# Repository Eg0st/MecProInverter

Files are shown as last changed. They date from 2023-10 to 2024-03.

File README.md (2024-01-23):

# Goal
This project is a student project at the Munich University of Applied Sciences.
The aim is to build and operate an inverter with an output of 3.6 kW,
which is supplied with 230 volts and can operate a motor in the frequency range of 10 to 500 Hz.
The ESP32-S3 and the SimpleFoc Bilbiotek were used for this.

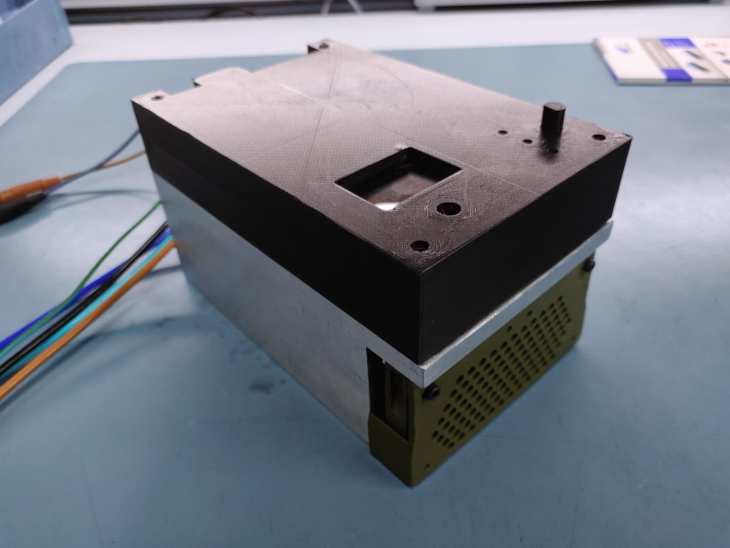
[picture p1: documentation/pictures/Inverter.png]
Inverter


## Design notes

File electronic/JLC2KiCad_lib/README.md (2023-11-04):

# MecProInverter

## ECAD Library
The Library is generatet via JLC2KiCad python skript from the JLCPCB assembly library. 
https://github.com/TousstNicolas/JLC2KiCad_lib

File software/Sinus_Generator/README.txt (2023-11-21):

Kleine Sinus Generator Klasse

erstellt einen Sinus, von -+256, es werden Werte von 0 bis PI/2 erstellt
die restliche Berechnung erfolgt unter Ausnutzung des Zweierkomplements,
da es ein periodisches Signal ist

Zweck: Vergleich für einen PWM Timer, um die Drehzahl abzulaufen

PS: wenn einer einen Plan hat wie man einen Konstruktor constexpr anlegt,
mir gerne Bescheid sagen ;D

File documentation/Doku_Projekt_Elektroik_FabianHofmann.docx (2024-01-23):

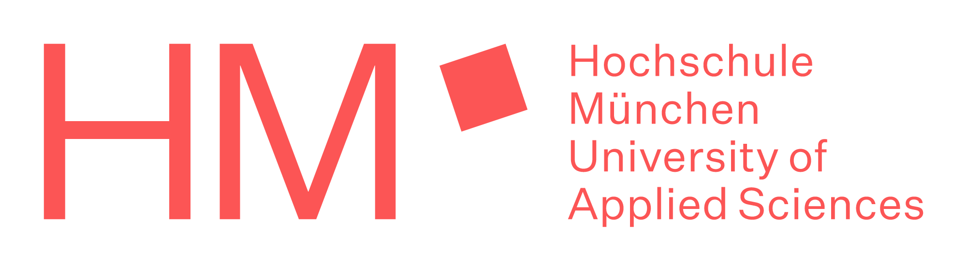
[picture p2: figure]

# Mechatronik Projekt- Entwicklung und Herstellung eines Umrichters für Drehstrommaschinen

Fabian Hofmann: Mechanik – Thermische Belastung und Gehäuse

# Elektronik

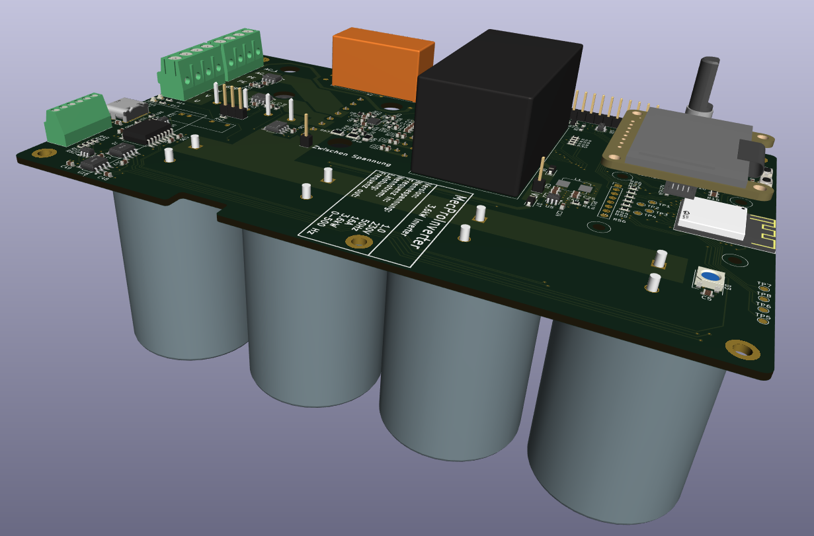
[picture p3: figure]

# 1. Abbildungsverzeichnis

# 2. Einführung

## Ziele

Ziel dieses Projektes war die Entwicklung und der Bau eines 3,6 kW Wechselrichters. Dieser sollte folgende Anforderungen erfüllen.

- Eingangsleistung von 3,6 kW (einphasig)
- Ausgang drei Phasen
- Ausgangs Frequenz variable von 10 bis 500 Hz
- Professionale Verarbeitung

Das gesamte Projekt wird Open Source sein, so dass Interessierte das Projekt replizieren können. Das Projekt ist in folgenden GitHub Repository vollständig einsehbar: https://github.com/Eg0st/MecProInverter

Da das Konzept einige Besonderheiten aufweist, sollte vor der Inbetriebnahme das Kapitel „Inbetriebnahme“ gelesen werden.

## Lösungsansatz

Der Inverter basiert auf einer 3-Fach-Halbbrücke. Dabei wird die Wechselspannung zunächst über einen Brückengleichrichter gleichgerichtet und in den Zwischenkreiskondensatoren, hier mit C1 bezeichnet, geglättet. Anschließend wird aus der Gleisspannung mit der 3-Fach-Halbbrücke ein sinuskommutiertes PWM-Signal erzeugt. Wird dieses Signal auf einen Drehstrommotor gegeben, so erzeugt die große Induktivität in dem Motor einen Sinus aus der PWM.

Abbildung 1 Konzept Plan

Für die Steuerung sind weitere Komponenten wie z.B. ein Mikrocontroller erforderlich.

# 3. Konzepte

## GitHub Repository

Die kompletten Daten sind im GitHub Repository verfügbar. Hier befindet sich die komplette Elektronik in den Ordnern „MecProInverter\electronic“. Das KiCad Projekt befindet sich im Ordner „MecProInverter\electronic\MecProInverter“. Die verwendeten Bibliotheken befinden sich in den Ordnern own_library und JLC2KiCad_lib. Own_library enthält alle selbst erstellten Bibliotheken und JLC2KiCad enthält alle Bibliotheken, die über das Phython Skript JLC2KiCad erstellt wurden. Dieses Skript ermöglicht es von Komponenten von JLCPCB eine Bibliothek für KiCad herunterzuladen.

## Isolationskonzept

Um die Kosten niedrig zu halten, wurde beschlossen, die gesamte Elektronik bis auf wenige Ausnahmen nicht gegeneinander zu isolieren. Lediglich der USB-Anschluss und vier GPIO-Pins sind isoliert. Dies spart Kosten und Aufwand, ermöglicht aber trotzdem die Nutzung aller Funktionen. Daher muss das komplette Human-Interface gegen Berührung isoliert werden, um eine sichere Bedienung sicherzustellen. Das wird durch Plastik Verlängerungen der Taster etc. erreicht.

## Stromversorgung

Während des normalen Betriebes wird das ganze System über die Netzspannung versorgt. Jedoch werden für die Steuerung zwei Hilfsspannungen benötigt.

- 15 Volt
- 3,3 Volt

Aus der Netzspannung von 230 Volt werden mit Hilfe eines Fertigmoduls 15 Volt mit bis zu 1,2 Ampere erzeugt. Aus den 15 Volt werden mit einem DC/DC-Wandler 3,3 Volt erzeugt. Zusätzlich kann der 3,3 Volt Regler über den VBus des USB-Anschlusses versorgt werden.

## Auslegung Zwischen Kreis

Der Zwischenkreis wurde nachfolgender Formel ausgelegt. Es wurde mit einer Schaltfrequenz des IGBT von 10 kHz gerechnet.

C=1/(∆U)*I*t

Daraus ergibt sich eine erforderliche Gesamtkapazität von 3 mF. Um Kosten zu sparen und den Platz besser zu nutzen, wurden drei 1 mF 325 Volt Kondensatoren parallelgeschaltet. Zur Sicherheit wurde der Einbauplatz für einen vierten vorbereitet.

# 4. Schaltplan

Der Schaltplan ist in zwei Teile gegliedert. Ein Teil enthält die gesamte Leistungselektronik und der zweite Teil enthält die Steuerung und Kommunikation. Dazu wurden in KiCad 7.0 zwei Pages erstellt. Die Power Page enthält die Leistungselektronik und die Controller Page den Rest. Im folgenden Kapitel wird auf alle Schaltungskomponenten eingegangen wobei der Schalplan im GitHub Repository zu finden ist. Die Datenblätter zu allen verwendeten Komponenten befinden sich im GitHub Ordner „GitHub\MecProInverter\electronic\datasheet“.

## Controller

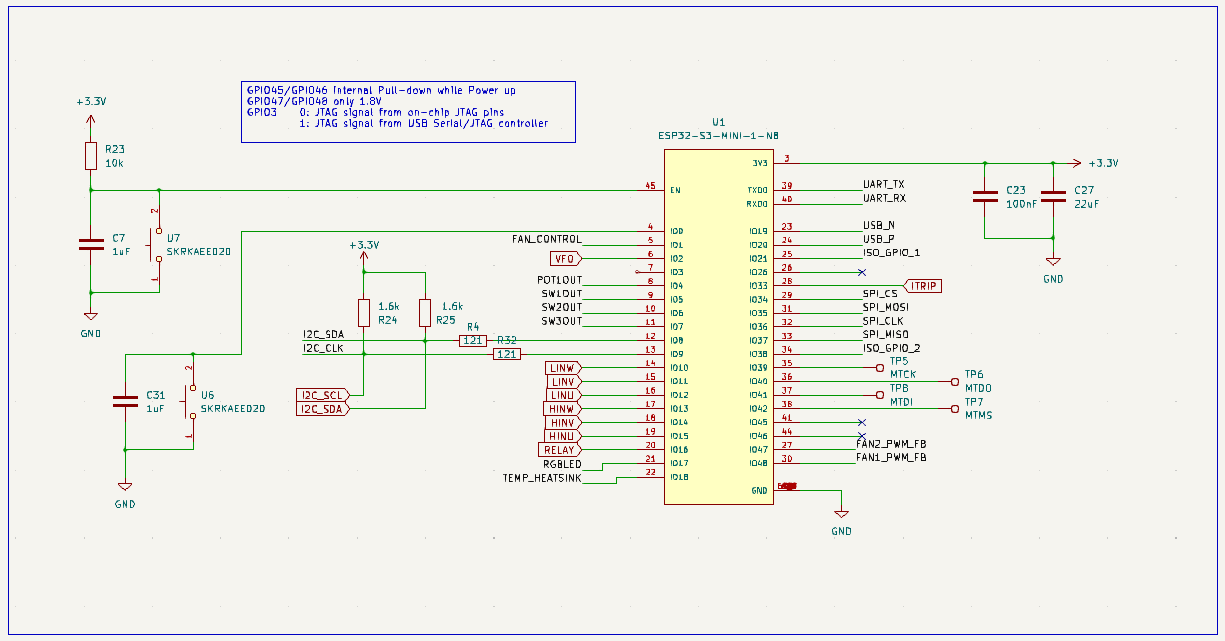
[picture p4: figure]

Abbildung 2 Mikrocontroller-Schaltung

Als Controller kommt der ESP-S3 Mini zum Einsatz. Dieser bietet neben dem notwendigen MPWM-Modul auch eine direkte USB-Schnittstelle. Dadurch kann auf einen Serial to USB-Konverter verzichtet werden. Am Enabele Pin befindet sich ein Reset Taster, der über einen Pull Up Widerstand auf High gehalten wird. Dadurch kann der Controller bei Bedarf neu gestartet werden. Darunter befindet sich am GPIO-Pin 0 der Mood Taster. Solange dieser beim Start des Controllers gedrückt wird, startet dieser in den Bootmodus und kann programmiert werden.

## Steuerung

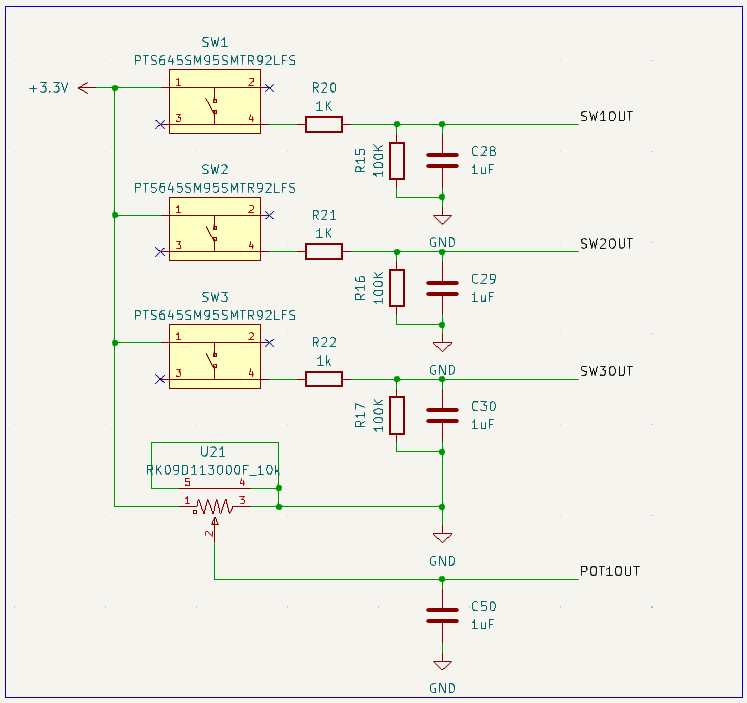
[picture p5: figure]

Abbildung 3 Steuerungs-Schaltung

Der Wechselrichter ist mit drei Tastern und einem Potentiometer zur Bedienung ausgestattet. Mit dem Potentiometer kann die Frequenz eingestellt werden. Die drei Taster sind für die restliche Steuerung und Navigation im internen Menü vorgesehen. Im Zusammenspiel mit dem Display soll es möglich sein, auch detailliertere Einstellungen vorzunehmen. Die Taster sind so beschaltet, dass sie den Pin des Controllers auf 3,3 Volt ziehen. Zusätzlich werden sie über ein RC-Glied entprellt. Dieses RC-Glied hat eine Einschaltverzögerung von 5 ms. Der Kondensator C50 sorgt dafür, dass die Spannung am Potentiometer geglättet wird.

## Anzeige

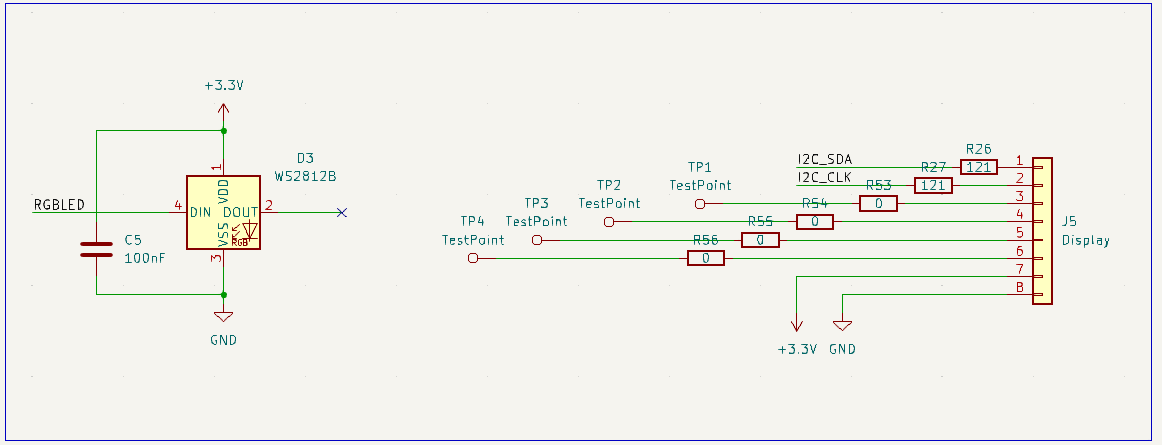
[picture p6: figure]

Abbildung 4 Anzeige-Schaltung

Der Inverter verfügt über ein Display und eine RGB-LED zur Statusanzeige etc. Die RGB-LED ist wie ein Schieberegister programmiert und kann über den DOUT mit weiteren LEDs verbunden werden. Zu beachten ist, dass der Betrieb der LED eine Versorgungsspannung von 3,5 Volt benötigt, es ist aber auch möglich, die LED mit 3,3 Volt zu betreiben. Für das Display wird ein I2C Display mit der Bezeichnung 938 der Firma Adafruit verwendet. Es handelt sich um ein 1“3 Zoll Oled Display.

## Kommunikation

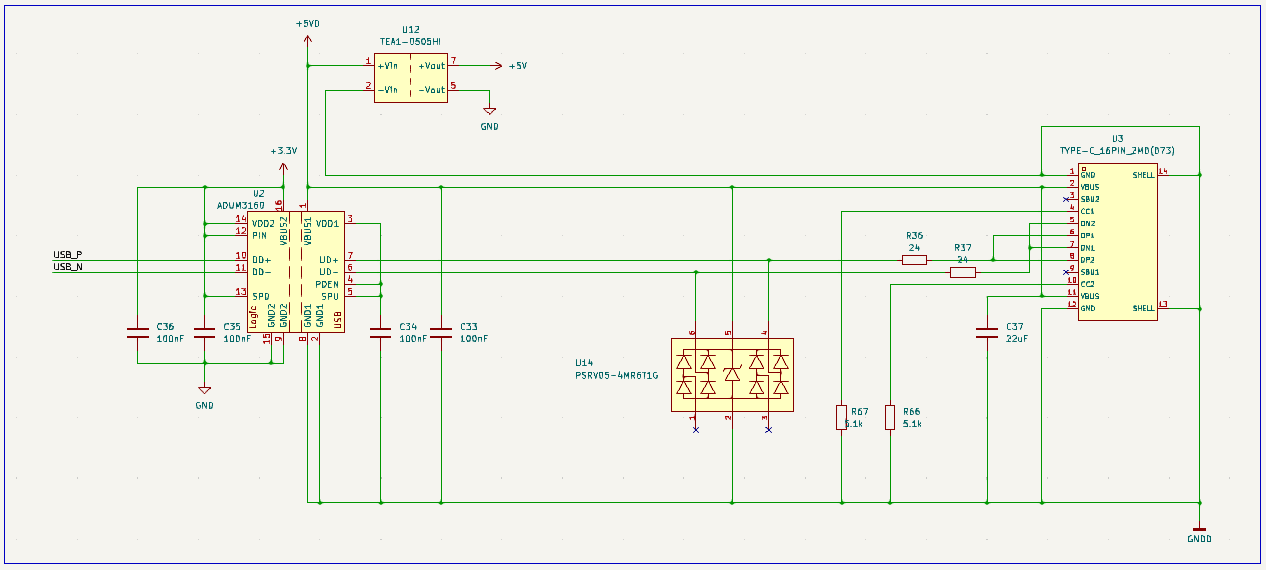
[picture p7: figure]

Abbildung 5 USB-C-Schaltung

Der Controller kann über eine isolierte USB-C-Buchse programmiert werden. Zusätzlich versorgt die USB-Schnittstelle über einen isolierten DC/DC-Wandler den 3,3 Volt Spannungswandler, so dass der Controller auch ohne zusätzliche Spannungsquelle betrieben und programmiert werden kann. Die isolierte USB-Schnittstelle bietet zudem den Vorteil, dass der Controller auch während des normalen Betriebs ausgelesen werden kann. Um einen Mindestschutz gegen ESD-Schäden zu gewährleisten, ist der USB-Eingang mit kurzangeschlossenen ESD-Dioden ausgestattet.

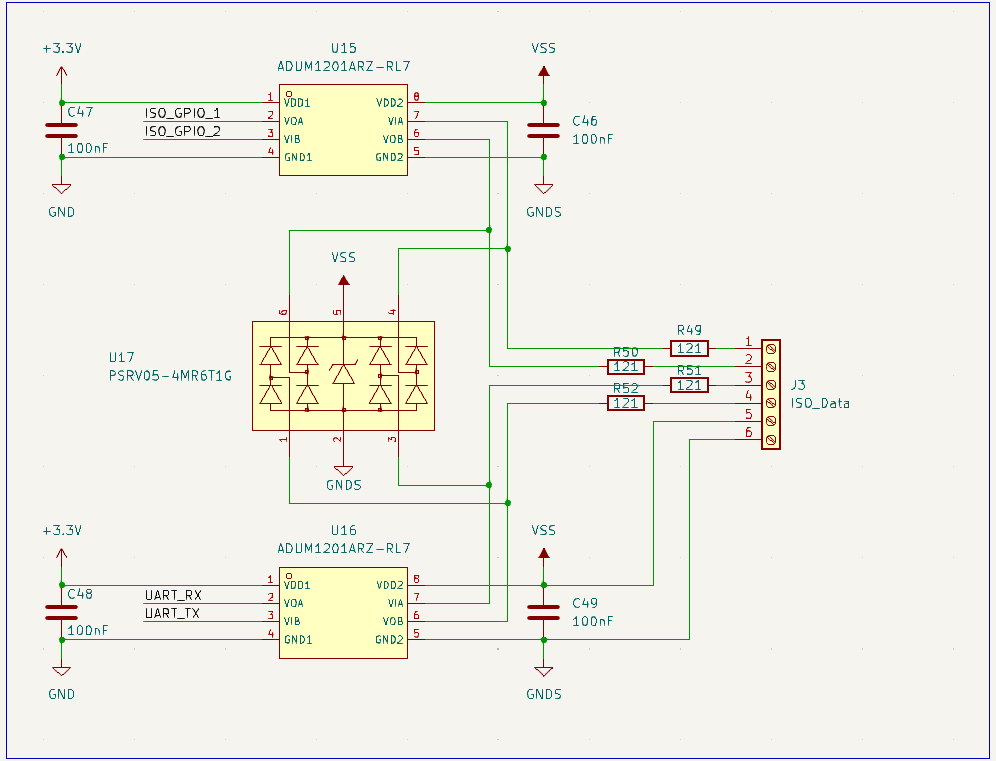
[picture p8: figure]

Abbildung 6 Isolierte GPIO Pin Schaltung

Neben der USB-Schnittstelle verfügt der Inverter über weitere isolierte Datenein- und -ausgänge. Darunter befinden sich eine UART-Schnittstelle sowie zwei freie GPIO-Pins. Da der ESP-32 eine freie Wahl der PINs für die Logikschnittstellen bietet, ist es somit möglich, an diesen beiden Pins eine isolierte I2C-Schnittstelle etc. zu realisieren. Diese Schnittstelle kann für eine externe Steuerung oder für einen externen Sensor verwendet werden. Eine weitere Anwendung wäre ein Not-Aus-Schalter.

## Lüfter Steuerung

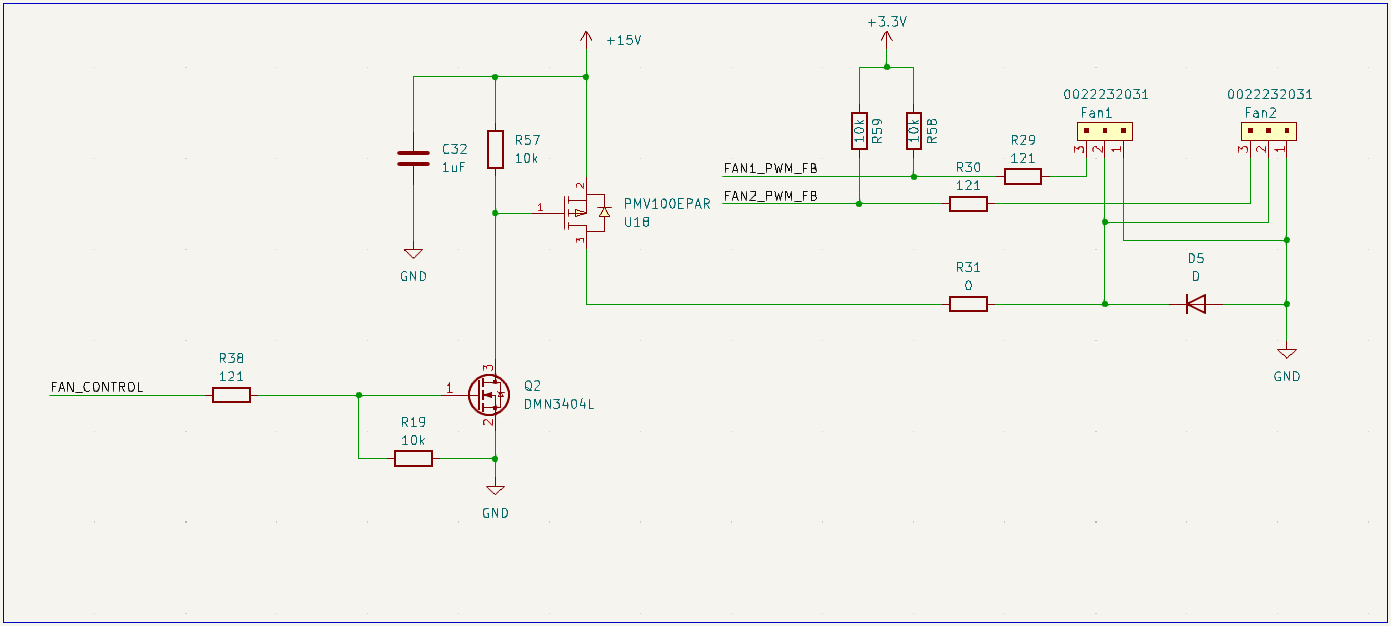
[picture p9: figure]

Abbildung 7 Lüftersteuerung-Schaltung

Die beiden Lüfter zur Kühlung des Kühlkörpers sind parallelgeschaltet und können daher nur synchron geschaltet werden. Jeder hat jedoch einen eigenen PWM-Rückmeldeausgang. Damit kann sichergestellt werden, dass kein Lüfterfehler vorliegt. Die Ansteuerung der Lüfter sollte zunächst über ein PWM-Signal erfolgen, jedoch ist eine normale PWM-Ansteuerung bei den verwendeten Lüftern nicht möglich, da diese eine reine Gleichspannung zum Betrieb benötigen. Zu beachten ist auch, dass die Lüfter Highside geschaltet werden müssen, da sonst der PWM-Regelkreis nicht funktioniert. R31 ist für den Fall vorgesehen, dass die Versorgung der Lüfter mit mehr als 15 Volt zu Störungen führt. Die Spannung kann durch einen Vorwiderstand auf 12 Volt reduziert werden.

## Pree-Charge

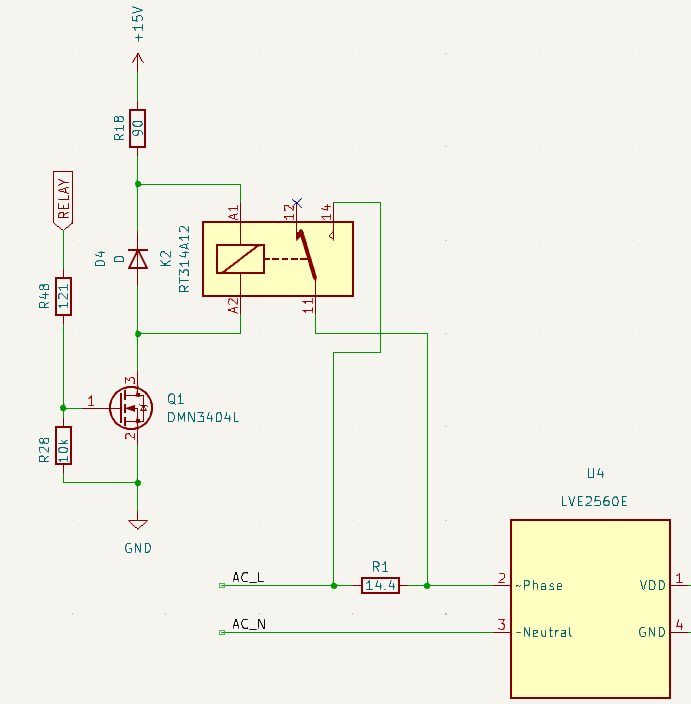
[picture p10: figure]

Abbildung 8 PreeCharge-Schaltung

Die Vorladung dient zur Begrenzung des Einschaltstromes beim Einschalten des Gerätes. Ohne Pre-Charging werden die Zwischenkreiskondensatoren direkt an die Netzspannung angeschlossen, diese stellen im ersten Moment einen Kurzschluss dar, wodurch der maximal mögliche Strom abfällt. Im schlimmsten Fall kann der hohe Strom die interne Schaltung des Zwischenkreises beschädigen. Deshalb werden die Kondensatoren über einen Widerstand geladen. Sobald die Kondensatoren geladen sind, wird der Widerstand durch ein Relais überbrückt. Andernfalls würde unnötig Energie verschwendet. Das Relais ist normal offen und wird vom Mikrocontroller über einen Mosfet auf der Lowside geschaltet. Die Diode D4 wird benötigt, um mögliche Rückinduktionsströme, die beim Abschalten des Relais entstehen, kurzzuschließen. R18 wird als Vorwiderstand benötigt, da es sich bei dem Relais um ein handelsübliches und somit kostengünstiges 12-Volt-Relais handelt.

## Messungen

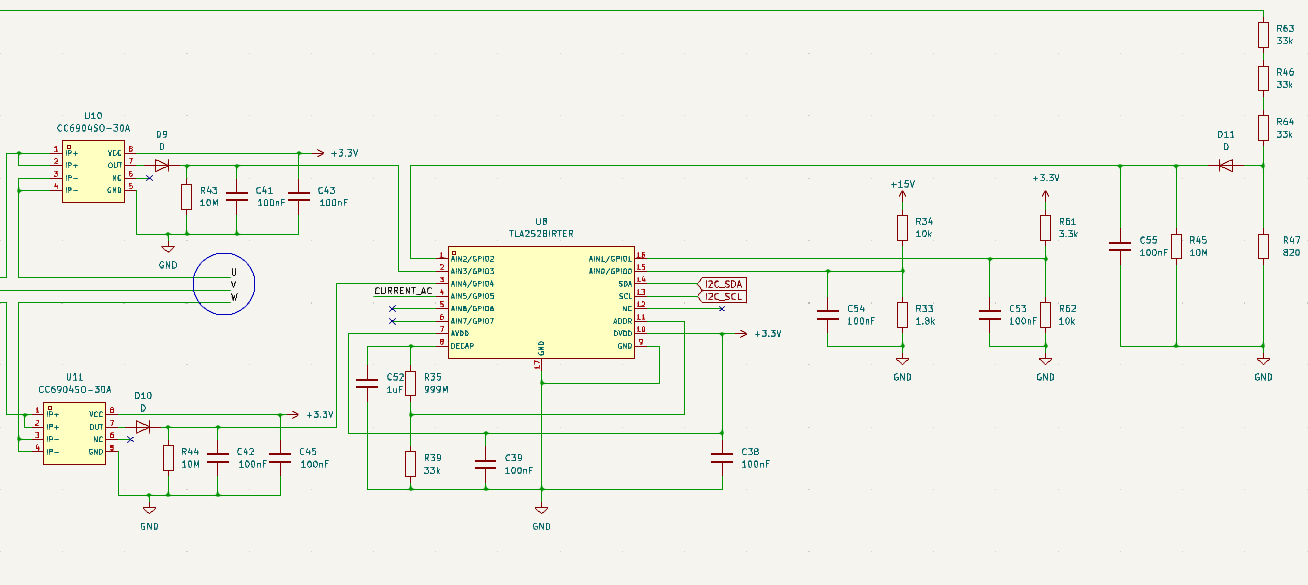
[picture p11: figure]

Abbildung 9 ADC und Hallsensor-Schaltung

Da der ESP32-S3 nur einen 12 Bit ADC mit großem Offset besitzt, wurde beschlossen, einen externen 8 Kanal ADC zu installieren. Dieser misst folgende Werte:

- Zwischenkreisspannung
- 3,3 Volt
- 15 Volt
- Eingangsstrom
- Ausgangstrom an der Phase U und W

Der ADC ist über I2C mit dem Mikrocontroller verbunden. Die Spannungsteiler für die Spannungsmessung sind so ausgelegt, dass sie bei Nennspannung eine Spannung von 2,5 Volt erzeugen. Außerdem besitzen sie alle einen Kondensator zur Spannungsglättung. Die Zwischenkreisspannung wird durch eine Diode und einen Kondensator gemessen. Der Widerstand R45 dient zur Entladung des Kondensators, um auch einen länger andauernden Spannungsabfall an der Zwischenkreisspannung messen zu können. Bei der Zwischenkreismessung wurden mehrere Widerstände in Reihe geschaltet, um die maximale Spannung der Widerstände nicht zu überschreiten.

Um den Strom auch auf der High Side messen zu können, werden Hallsensoren verwendet, die in Abhängigkeit vom Strom eine Spannung ausgeben. Da die verwendeten Sensoren einen Offset besitzen, kann mit ihnen auch ein negativer Strom gemessen werden. Diese Sensoren werden ebenfalls an den externen ADC angeschlossen. Mit dem Maschensatz kann der Strom der letzten Phase W genau berechnet werden.

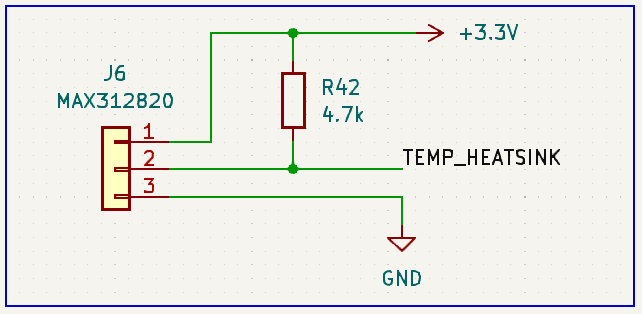
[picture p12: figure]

Zur Messung der Kühlkörpertemperatur ist zusätzlich ein Steckplatz für einen One-Wire Temperatursensor vorbereitet. Dieser wird jedoch nicht benötigt, da das verwendete Powermodul über einen internen Temperatursensor verfügt.

## Stromversorgung

Für den Betrieb der Schaltung sind zwei Hilfsspannungen erforderlich. Zum einen 15 Volt für den Betrieb des IGBT, des Lüfters und des Relais. Zusätzlich werden 3,3 Volt für den Betrieb des Mikrocontrollers und der Peripherie benötigt. Aus den 230 Volt Wechselspannung werden also mit einem fertigen Modul 15 Volt erzeugt. Aus diesen werden dann über einen DC/DC-Wandler 3,3 Volt erzeugt. Zusätzlich ist es möglich, den 3,3 Volt DC/DC Wandler über die 5 Volt des USB-Anschlusses zu versorgen. Dazu wurden Dioden so eingebaut, dass sich die beiden Spannungsquellen nicht gegenseitig beeinflussen. J9 ist ein Messpunkt für.

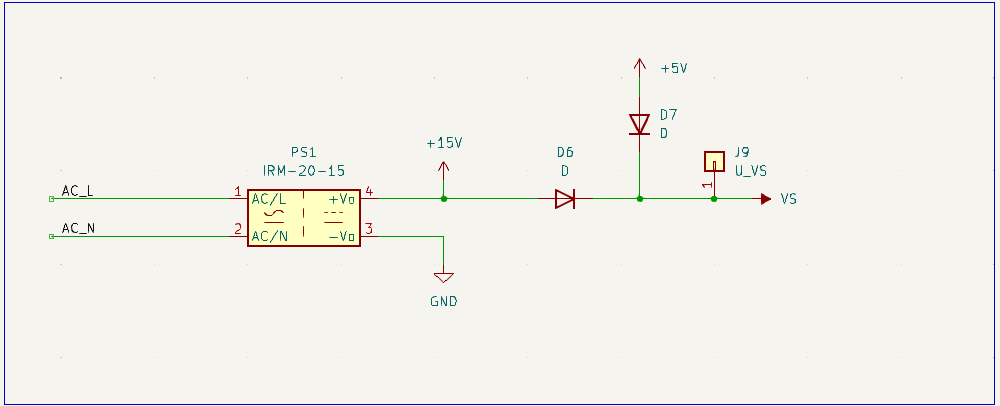
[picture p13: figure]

Abbildung 10 Parallelschaltung Stromquellen-Schaltung

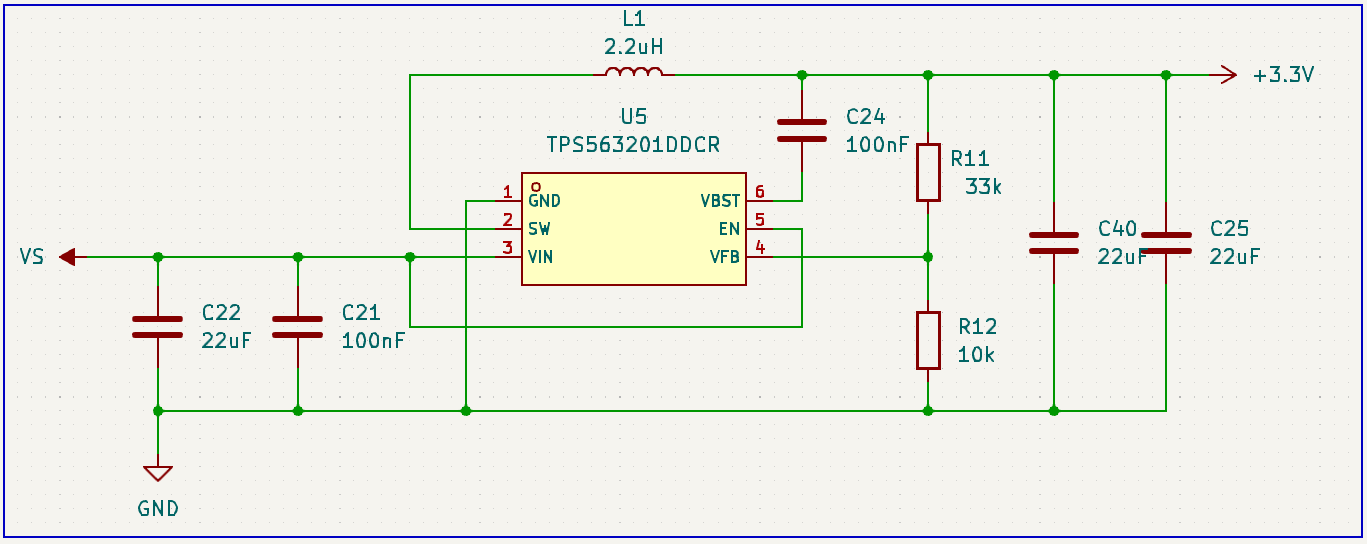
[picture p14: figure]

Abbildung 11 3,3 Volt Regler-Schaltung

Der Aufbau der 3,3 Volt DC/DC Wandler (TPS563201DDCR) ist dem Datenblatt entkommen. Die Spannung kann mithilfe der Widerstände R11 und R12 eingestellt werden.

## IGBT

Als Leistungsmodul kommt der IKCM20L60GA der Firma Infineon zum Einsatz. Dabei handelt es sich um eine Triple-H-Brücke mit integriertem Treiber. Dies hat den Vorteil, dass für den Betrieb nur eine minimale Anzahl von Bauteilen benötigt wird. Zusätzlich bietet das Modul die Möglichkeit, den aktuellen Betriebszustand bzw. die Temperatur über einen analogen Pin auszulesen. Zusätzlich kann über den ITRIP-Pin eine Strombegrenzung realisiert werden. Im Projekt wird der Pin direkt vom Mikrocontroller angesteuert, um das Modul im Fehlerfall abzuschalten.

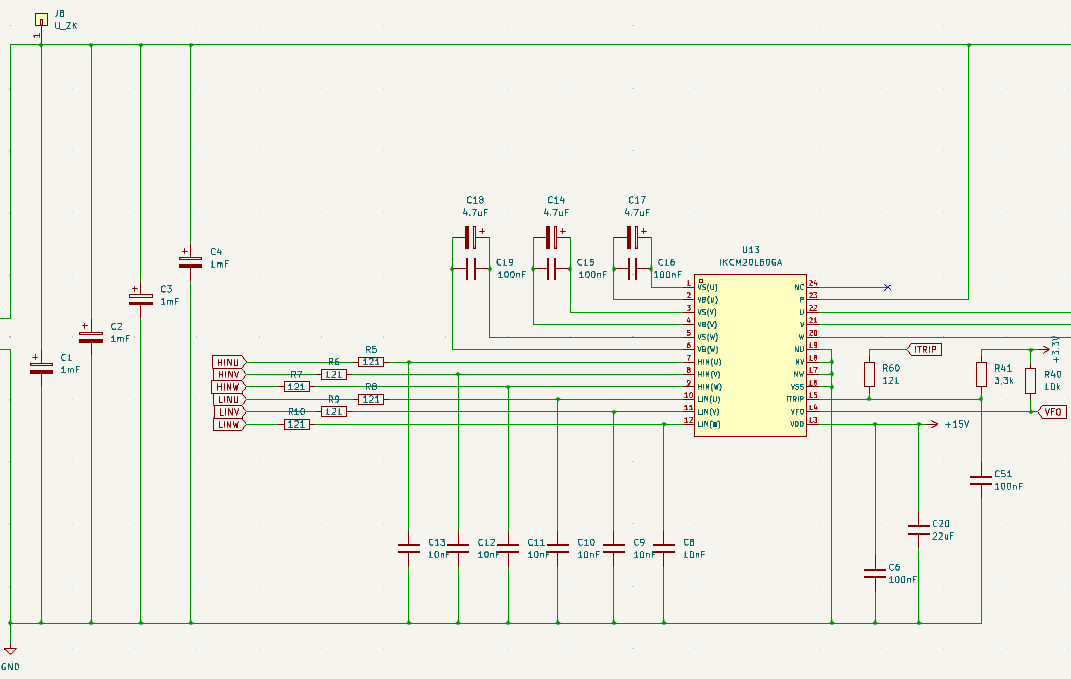
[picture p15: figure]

Abbildung 12 IGBT-Schaltung

C1 bis C4 sind die Zwischenkreiskondensatoren und werden über das Netz auf ca. 325 Volt geladen. Die einzelnen MosFests werden über HINU, HINV, ... angesteuert. Diese haben eine Strombegrenzung, die mit Widerständen realisiert ist, um den Mikrocontroller zu schonen. C14 bis C19 dienen als Kondensator zur Erzeugung der Spannung zum Schalten der Highside Kondensatoren. Diese werden aufgeladen, wenn die Low Side Gates durchgeschaltet werden. Daher ist es nicht möglich, die High Side Gates von Anfang an durchzuschalten. Die weitere Schaltung ist dem Datenblatt bzw. der Application Note zu entnehmen.

# 5. Layout

Das Layout wurde in KiCad erstellt. Das Layout besteht aus 4 Ebenen. In der Darstellung ist die Oberseite rot und die Unterseite blau dargestellt. Die Zwischenlängen wurden hauptsächlich als Grundriss und für die Spannungsversorgung verwendet. Die Spannungsversorgung ist hier jedoch je nach Bedarf in mehrere Bereiche unterteilt. Zusätzlich befindet sich in der rechten oberen Ecke ein Isolierbereich für isolierte Anschlüsse. Der Isolationsabstand zwischen den einzelnen Spannungsebenen beträgt 0,8 mm. Zu den isolierten Bereichen sind Abstände von 4 mm vorgesehen.

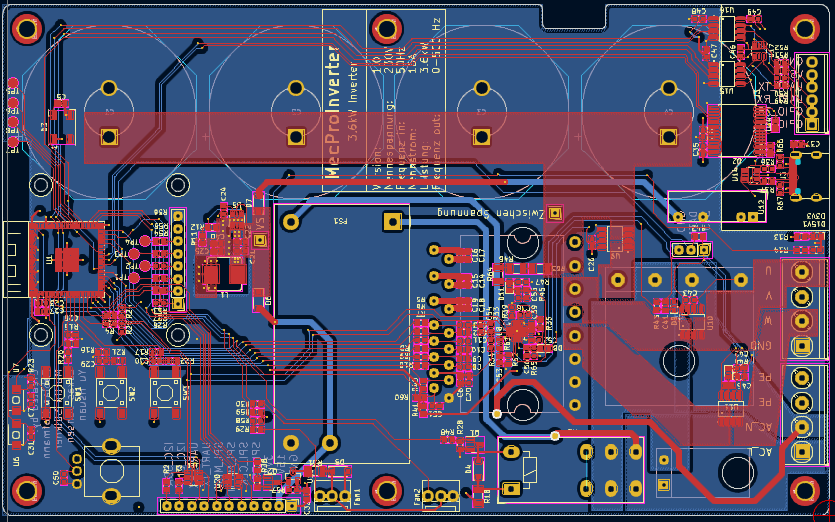
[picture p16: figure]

Abbildung 13 Layout (Ohne Zwischen Lagen)

Die Platine ist so aufgebaut, dass die einzelnen Komponenten wie Leistungselektronik, DC/DC-Wandler, Logikschaltungen möglichst getrennt sind.

Zu beachten ist auch, dass sich unterhalb der Antenne des ESP32-S3 keine Platine befinden darf, da dies die Performance des WLAN-Moduls beeinträchtigt. Für die mechanische Befestigung der Leistungsbauteile auf dem Kühlkörper sind zusätzliche Bohrungen vorgesehen. Die Aussparung auf der Oberseite dient als Kabeldurchführung für die Lüfter.

Es ist jedoch zu beachten, dass der Footprint des Brückengleichrichters nicht korrekt ist. Dieser ist seitenverkehrt und muss für eine V2 überarbeitet werden.

# 6. Inbetriebnahme

Die erste Inbetriebnahme ist durch Einstecken des USB-Steckers möglich. Dabei sollte bereits die 3,3 Volt LED aufleuchten. Außerdem sollte es möglich sein, den Micocontroller zu programmieren und die IOs anzusteuern.

Im nächsten Schritt kann über den 15 Volt Pin eine externe 15 Volt Spannungsquelle angeschlossen werden. Nun können die Lüfter, das Relais und der IGBT angesteuert werden und die 15 Volt LED sollte leuchten. Wird nun eine Spannung über den Zwischenkreis-Pin eingespeist, kann der IGBT am Ausgang getestet werden. Dabei ist zu beachten, dass zum Ansteuern der High-Treiber des IGBTs zunächst der Versorgungskondensator für die Treiber aufgeladen werden muss. Dies geschieht, sobald die Low-Treiber der einzelnen Phasen durchgeschaltet sind. Um den IGBT zu testen, ist es daher sinnvoll, ein PWM-Signal anzulegen. Um die Ausgänge des IGBT zu aktivieren, muss der ITRIP-Pin auf Low gesetzt werden.

Im letzten Schritt können 230 Volt angelegt werden. Dabei muss jedoch die 15 Volt Hilfsspannung abgeschaltet werden. Dabei ist zu beachten, dass der Vorladewiderstand ggf. über den Kühlkörper gekühlt oder anderweitig überbrückt werden muss. Alternativ kann die Spannung durch einen regelbaren Trenntransformator etc. langsam erhöht werden.

Da der USB-Anschluss isoliert ist kann bei jedem Schritt der Status des Inverters über den Micocontroller überwacht werden.

# 7. Tests

Alle Komponenten mit einer Versorgungsspannung von bis zu 15 Volt wurden auf Funktion getestet. Alles funktionierte wie erwartet und sind deshalb nicht interessant. Daher wird in diesem Kapitel nur Versuche dokumentiert, die bei höheren Spannungen durchgeführt wurden. Es wurden folgende zwei Versuche durchgeführt.

## Versorgung über 230 Volt an einem Trenntransformator

Der Wechselrichter wurde an den Trenntransformator angeschlossen und die Spannung langsam erhöht. Damit sollte sichergestellt werden, dass die Spannungsversorgung funktioniert und kein Kurzschluss vorliegt. Dazu wurde die Zwischenkreisspannung extern mit einem Multimeter gemessen.

Es ist zu beobachten, dass die Spannung am Zwischenkreis mit steigender Eingangsspannung zunimmt. Wobei diese um einen Faktor von ca. 1,4 höher ist. Dies ist auf die Gleichrichtung der Wechselspannung zurückzuführen. Ab einer Spannung von ca. 100 Volt schaltet der 15 Volt und 3,3 Volt Spannungskreis. Eine weitere Erhöhung der Spannung führt nur zu einer Änderung der Zwischenkreisspannung.

## Ansteuerung des IGBT bei 100 V mit PWM-Sinuskommutierung

In diesem Versuch soll die PWM-Sinuskommutierung am Ausgang des IGBT überprüft werden. Dazu wird der Wechselrichter über einen Trenntrafo mit Spannung versorgt. Die Spannung wird so gewählt, dass alle Komponenten funktionieren (15 Volt Regler). Nun wird mit Hilfe eines Oszilloskops der unbelastete Ausgang des Wechselrichters betrachtet. Dabei wurden die einzelnen Phasen es Ausgangs gegen Masse dargestellt.

Die folgenden Spannungsverläufe wurden zu verschiedenen Zeitpunkten aufgezeichnet. Am Zwischenkeil wurde eine Spannung von 100 Volt gemessen.

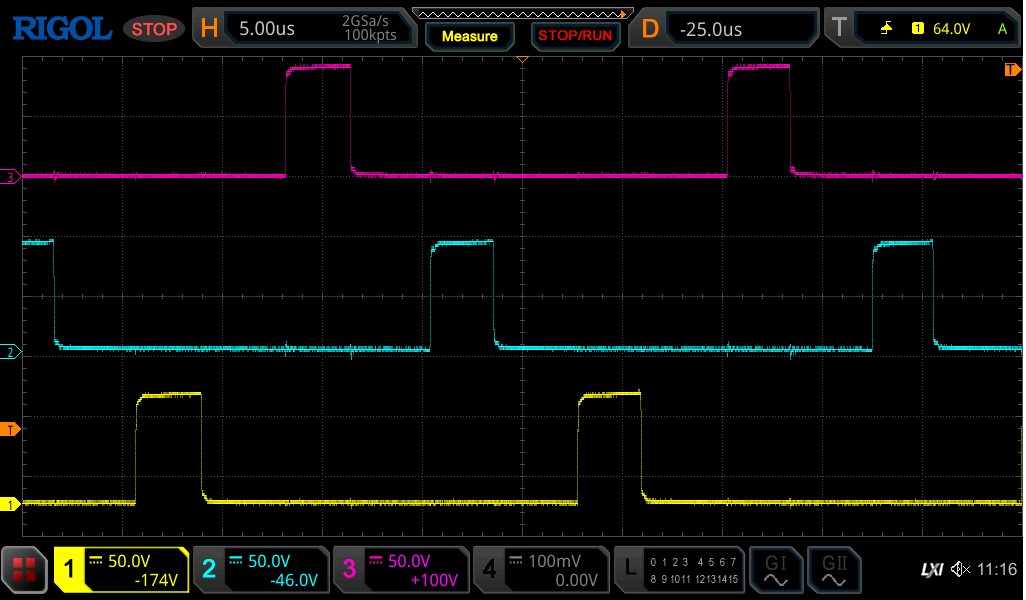
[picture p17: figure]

Abbildung 14 Testergebnis Einschaltdauer ca. 20

Es ist gut zu erkennen, dass der IGBT bis zu den 100 Volt des Zwischenkreises voll durchschaltet und auch gegen Masse schaltet.

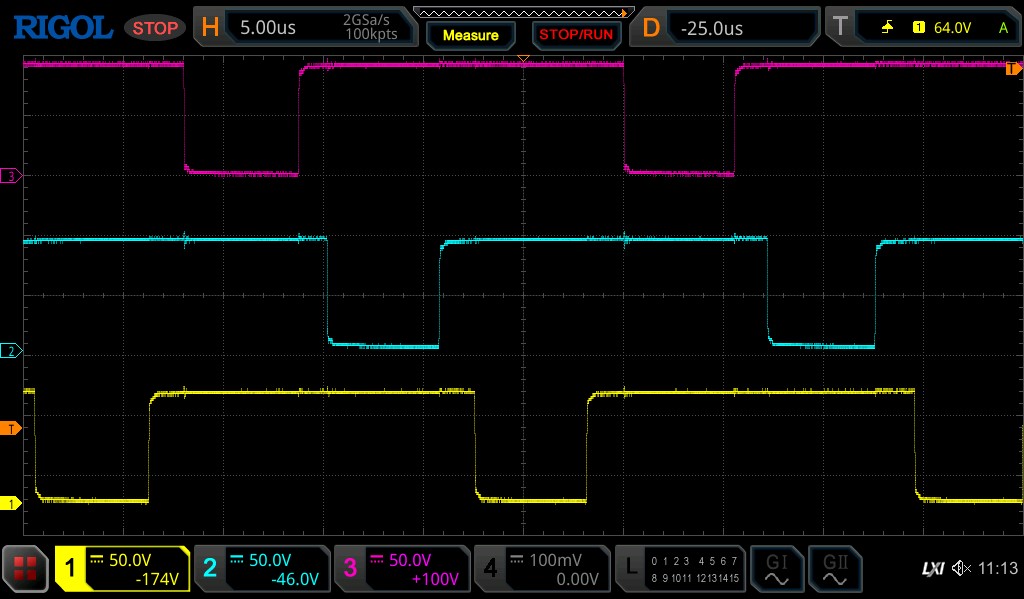
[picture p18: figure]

Abbildung 15 Testergebnis Einschaltdauer ca. 80

Dieser Abschnitt wurde zu einem späteren Zeitpunkt hinzugefügt. Durch die Änderung der Steuerzeiten ist anzunehmen, dass die PWM-Sinuskommutierung funktioniert.

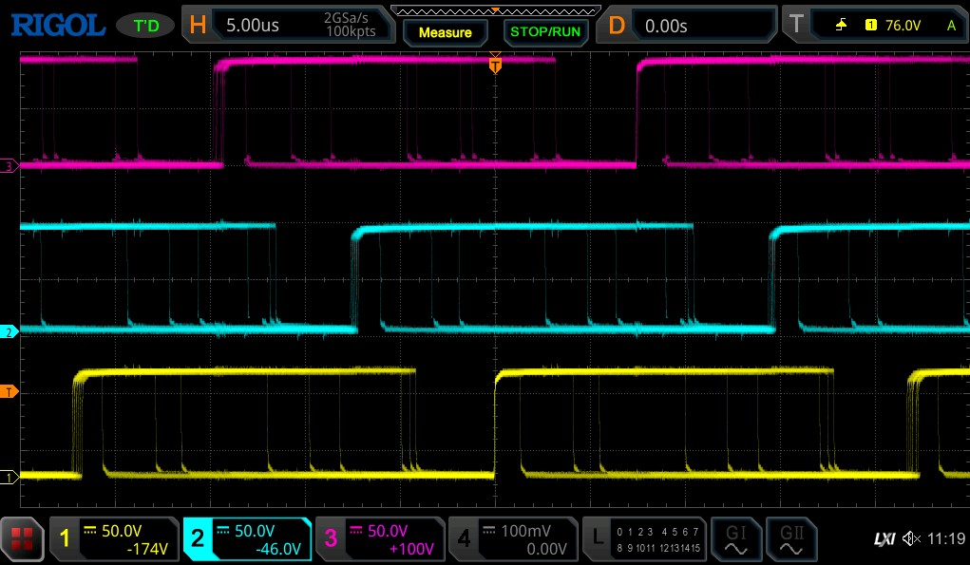
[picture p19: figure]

Abbildung 16 Testergebnis Duty Cycle sweep

Diese Abbildung zeigt eine Überlagerung über einen längeren Zeitraum. Es ist gut zu erkennen, dass die PWM über den gesamten Zeitraum variiert.

Diese Ergebnisse zeigen, dass der Betrieb auf einem Motor sicher funktioniert. Aus Zeitgründen konnte dieser Versuch jedoch nicht durchgeführt werden.

# 8. Ausblick

Derzeit befindet sich der Wechselrichter in einem nicht vollständig getesteten Zustand. Außerdem enthält das Layout einen Fehler im Footprint des Brückengleichrichters (siehe Kapitel Schaltplan). Die Versuche lassen erwarten, dass der Betrieb des Motors keine Probleme bereitet.

Sollte das Projekt weiterentwickelt werden, wird empfohlen, eine zweite Version der Platine zu erstellen, die einen deutlich kompakteren 15-Volt Regler besitzt. Dies ermöglicht auch eine Vergrößerung der Isolationsabstände. Außerdem sollte eine automatische Entladung der Zwischenkreiskondensatoren realisiert werden, da dieser bis zu 5 Minuten zum Entladen benötigt, was ein gewisses Risiko darstellt. Auch eine Überarbeitung der Anschlussklemmen mit größeren Phasenabständen etc. kann zur Verbesserung der Sicherheit beitragen. Eine weitere Überlegung ist die Erhöhung der Leistung durch Umstellung der Stromversorgung auf Drehstrom.

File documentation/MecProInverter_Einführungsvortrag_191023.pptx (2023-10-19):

## Einführungspräsentation Projekt Mechatronik

von Fabian Hoffmann, Lukas Jansen, Martin Sölkner, Yu-Hsuan Cheng

## Funktion eines Asynchronmotors

Fakultät für Elektro- und Informationstechnik

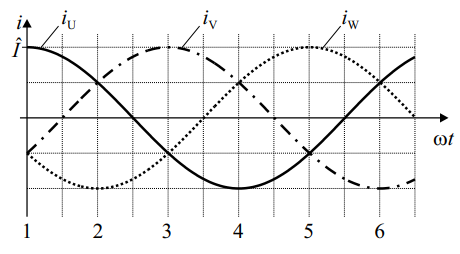
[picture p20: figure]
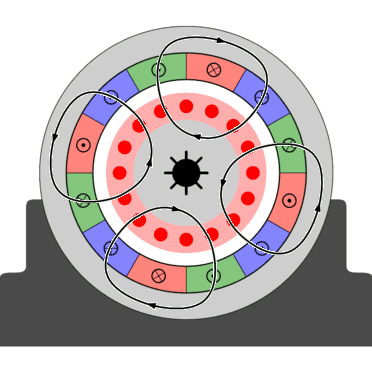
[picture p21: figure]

Stator

Drehfeldwicklung

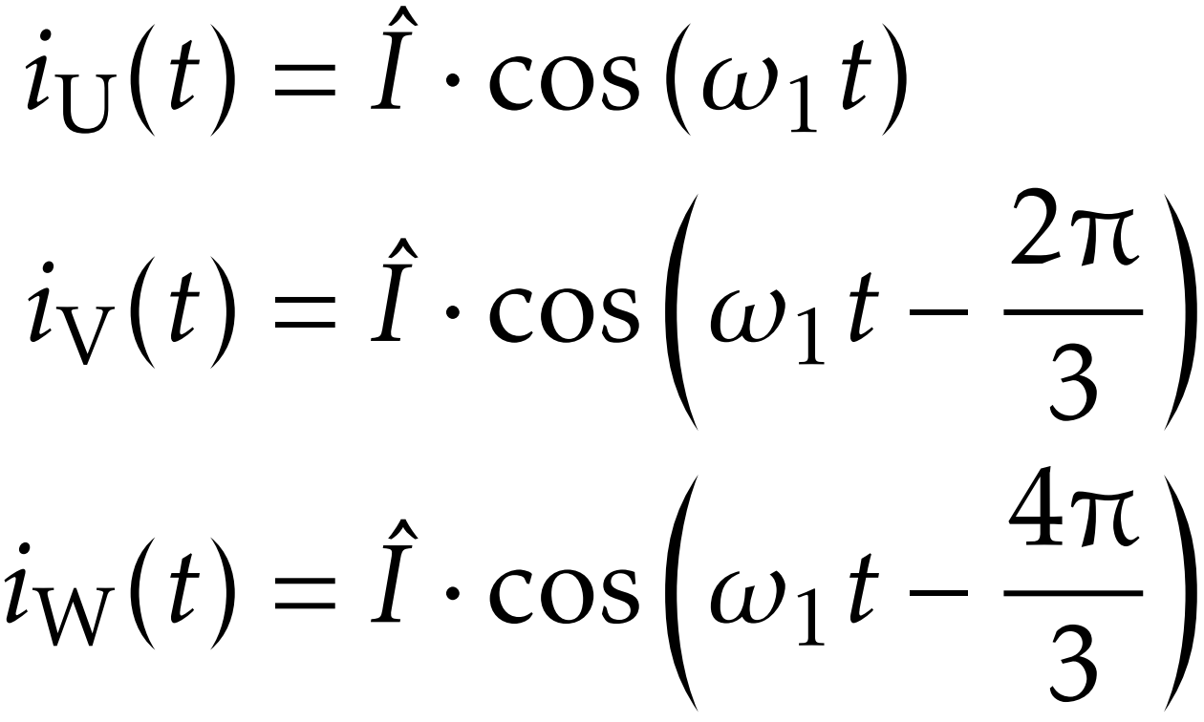
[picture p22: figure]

Rotor (Käfig)

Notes: Funktion eines Asynchronmotors:
Drehfeld im Stator und Rotor als Käfig (kurzgeschlossen)
Drehfeld immer schneller laufen, als Rotor (Käfig)
Induktion eines Stroms
Erzeugung einer Kraft (Lorentzkraft)

Drehfeld aus Strom erzeugt:
magnetische Flussdichte ∝ Strom

Sinusförmiger Strom pro Phase => um 120 Grad phasenversetzt


B=c∗i_U (t)∗cos(π/(τ_P)∗x)

τ_P = Polteilungszahl
x = Rotorhilfswert
c = Maschinenkonstante
i_U (t)=zeitlicher Strom
Funktion eines Asynchronmotors:
Drehfeld im Stator und Rotor als Käfig (kurzgeschlossen)
Drehfeld immer schneller laufen, als Rotor (Käfig)
Induktion eines Stroms
Erzeugung einer Kraft (Lorentzkraft)

Drehfeld aus Strom erzeugt:
magnetische Flussdichte ∝ Strom

Sinusförmiger Strom pro Phase => um 120 Grad phasenversetzt


B=c∗i_U (t)∗cos(π/τ_P ∗x)

τ_P = Polteilungszahl
x = Rotorhilfswert
c = Maschinenkonstante
i_U (t)=zeitlicher Strom

## B6-Brücke

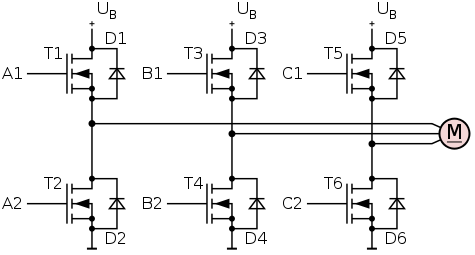
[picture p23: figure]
Datei:3-Fach-Halbbrücke mit FET.svg
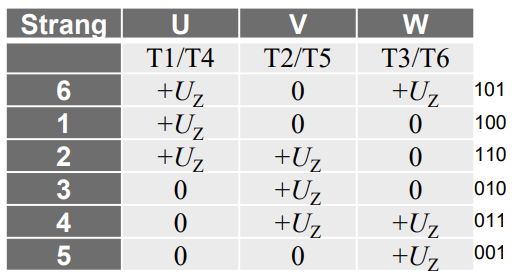
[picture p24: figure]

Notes: B6 Brückenschaltung aus abschaltbaren Halbeitern (pro Phase eine Halbbrücke)

Steuert die drei Phasen an

Es gibt 6 Stellungen die benötigt werden

Drehfeld bewegt pro Stellung um 60 Grad weiter

## Pulsweitenmodulation

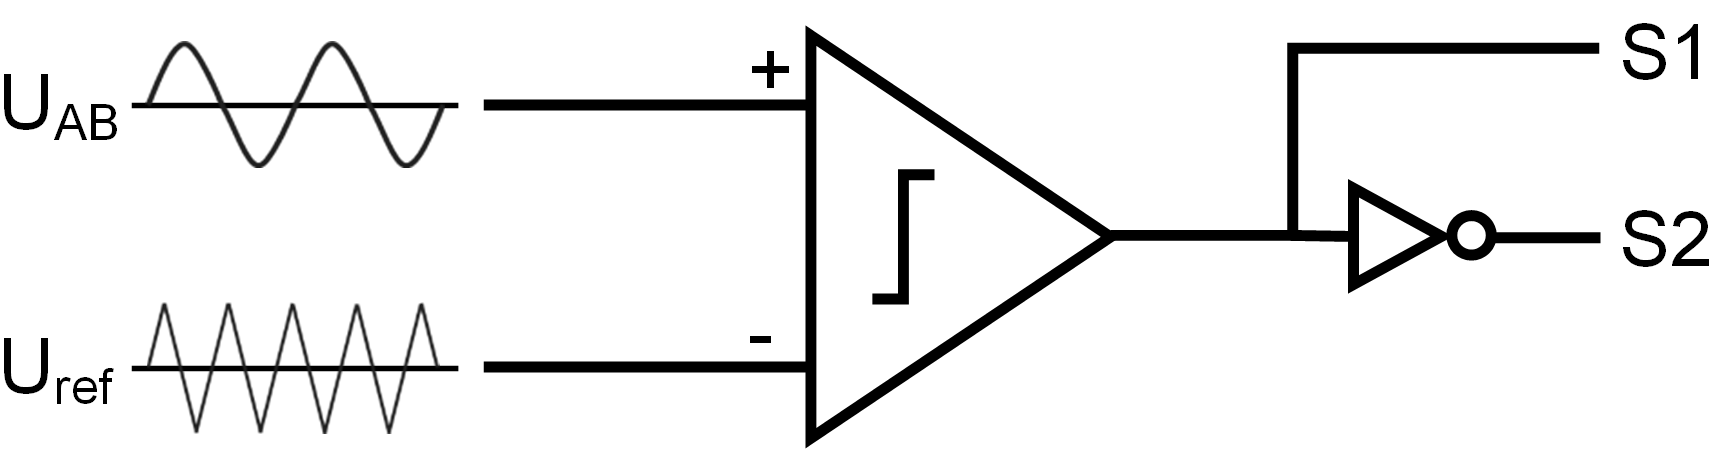
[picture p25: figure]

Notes: Einfachste Form ist es in einem Komparator einen Sinus und ein Trägersignal anzulegen

Trägersignal ist ein Dreieckssignal mit höherer Frequenz als das Grundsignal

bei Überschneidungen wird ein Puls ausgegeben zwischen 0 und 1

Bei Einbau eines Drehzahlsensor + Aufbau eines Regelkreis mit der Drehzahl als Führungsgröße

=> Reglung des Motors

## Pulsweitenmodulation


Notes: Durch ein Transportsignal und einem Referenz Sinus wird ein PWM erzeugt

Ziel ist es einen Sinusförmigen Strom in den jeweiligen Phasen des Stator zu erzeugen

Die Sinus sind pro Phase um jeweils 120 Grad phasenversetzt

Durch die Spule kann der Strom nicht springen somit wird ein Sinus erzeugt

Umso höher die Frequenz desto weniger rippliger ist das Stromsignal

Allerdings führen höhere Schaltfrequenzen zu höheren Umschaltverlusten

Asynchronmaschine funktioniert nur mit sinusförmigen Strömen (Sinuskommutierung), da sonst wegen des großen
Oberschwingungsgehaltes der Speisung => hohe Eisenverluste

## Danke für Ihr Interesse!

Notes: Vielen Dank für euer und für Ihr Interesse.

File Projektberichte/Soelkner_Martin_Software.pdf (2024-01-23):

Hochschule München

### Projektbericht im Fach “Projekt Mechatronik“

### Implementierung einer Steuerung für einen Inverter

Gruppe: Software
Name: Martin Sölkner
Studiengruppe: ELM1
Übersicht

Der vorliegende Code hat das primäre Ziel, einen Inverter zu steuern. Zu Beginn wurde eine

umfassende Analyse durchgeführt, um die spezifischen Anforderungen und Aufgaben der

Software des Inverters zu bestimmen. Diese umfassten eine phasenkorrekte Sinus-

Kommutierung | sowie | eine | Zustandsmaschine | (State | Machine). | Die | anfängliche

Implementierung basiert auf dem Open-Loop-Modus. Die Zustandsmaschine wurde so

konzipiert, dass sie fünf Zustände aufweist.

Die Implementierungsstrategie folgte dem objektorientierten Ansatz, bei dem nahezu jede

Aufgabe in einer eigenen Klasse gekapselt wurde. Dort, wo ein objektorientierter Ansatz

nicht zielführend schien, wurde ein Namensraum (Namespace) verwendet.

Strukturierung des Programmcodes

Der Code wurde strukturiert, indem funktionell zueinander gehörende Elemente in separate

Quellcodedateien (Source Files) aufgeteilt wurden. Die Struktur ist wie folgt gestaltet:

- | conf.hpp: | Diese | Datei | enthält | sämtliche | Makros, | die | sich | auf | Eingänge,

Maschinenkennwerte und Businformationen beziehen.

- foc_pwm.hpp: Diese Datei umfasst die Funktionen der feldorientierten Regelung (Field

Oriented Control - FOC). Zusätzlich beinhaltet sie eine Klasse für den Zeitgeber (Timer),

der das Auslesen der Sensoren zeitlich steuert.

- interface.hpp: Die in dieser Header-Datei enthaltene Struktur dient dem Datenaustausch

zwischen den Klassen. Sie enthält die Zeigerdeklarationen für die einzelnen

Sensorklassen und Busse sowie wichtige Variablen.

- IState.hpp: Diese Interface-Klasse dient als Oberklasse für alle Zustandsinstanzen.
- sensor_func.hpp: Diese Header-Datei enthält die Methoden für die Sensoren,

einschließlich des ADC und des Temperatursensors, sowie eine Funktion zum Auslesen

des Potentiometers.

- Tstate_machine.hpp: Diese Klasse stellt die Oberklasse der Zustandsmaschine dar. Sie

verwendet Templates, um eine Code-Wiederverwendbarkeit zu ermöglichen.

- state_machine.hpp: Diese Klasse erbt von der Klasse TState_Machine und spezifiziert

die Zustandsmaschine durch spezifische Attribute sowie Methoden, die ausschließlich für

diese bestimmte Zustandsmaschine entwickelt wurden. Darüber hinaus enthält sie die

Zustandstabelle (State-Transition Table), welche die Kontrolle der einzelnen Zustands-

übergänge (State Transitions) ermöglicht.

- states.hpp: In dieser Header-Datei sind die einzelnen Zustandsklassen implementiert.

Diese Klassen erben von der Oberklasse ISTate, sodass alle Zustandsklassen dieselben

Methoden besitzen.

Umsetzung der einzelnen Module

Aufbau der State Machine

Bei diesem Projekt war die Entwicklung einer Zustandsmaschine, oder State Machine, eine

der zentralen Anforderungen. Im Rahmen des Betriebs der State Machine sind verschiedene

Zustände (States) vorgesehen. Diese sind in Abbildung 1 dargestellt.


Abbildung 1 - Übersicht über das Zustandsdiagramm

Der erste Zustand ist der Power_Up State. In diesem Zustand werden zunächst die beiden

Busse (One Wire und Two Wire) und anschließend die dazugehörigen Sensoren (ADC und

Temperatursensor) hochgefahren. Darüber hinaus finden in diesem Zustand bereits erste

Messungen mit der Peripherie statt.

Nach erfolgreicher Durchführung aller Prüfungen erfolgt der Wechsel in den Pre_Charge.

Hier wird die Zwischenkreisspannung UTank ständig gemessen. Sobald das Delta von ∆UTank

nicht weiter ansteigt, wird der Pre-Charge (Vorlade) - Widerstand durch ein Relay überbrückt

und es erfolgt ein Wechsel in den Standby Zustand.

Im Standby Zustand wird ein Timer aktiviert, der alle 500 Hz eine Messung startet, um alle

wichtigen Parameter zu überwachen. Dabei werden lediglich zwei Messwerte pro Zyklus

ausgelesen, um Interrupts zeitlich nicht zu blockieren. Darüber hinaus, wird ein Taster

ausgelesen, der im Falle der Betätigung in den Run Zustand wechselt.

Im Run Zustand kann entweder über einen Taster mit vordefinierten Werten oder über ein

Potentiometer die Drehzahl eingestellt werden. Durch Auslösen des Stopp Tasters erfolgt der

Wechsel zurück in den Standby Zustand.

Neben diesen Zuständen existiert ein Safety State. Dieser Zustand wird aktiviert, sobald ein

ungewöhnlicher Wert auftritt und führt zum sofortigen Stopp der Maschine. Dieser

Sicherheitszustand muss ausdrücklich vom Benutzer zurückgesetzt werden. Nach der

Rücksetzung wird die Maschine in den Pre_Charge Zustand versetzt und beginnt den

Hochfahrprozess erneut.

Implementierung der State Machine

Der ursprüngliche Ansatz basierte auf einer einfachen Switch-Case-Funktion, doch dieser

Ansatz stellte sich als problematisch heraus. Insbesondere die hintereinander Reihung von

mehreren Zuständen und deren Logiken beeinträchtigten die Wartbarkeit des Programms.

Darüber hinaus war es schwierig, die Kontrolle über die Zustandsübergänge, den sogenannten State Transitions, zu behalten. Ein Beispiel ist die Überprüfung, ob ein direkter

Übergang von Power_Up zu Run zulässig ist.

Zur Lösung dieser Herausforderungen wurde eine gekapselte Zustandsmaschine

implementiert. Diese Methode bietet den Vorteil, dass alle Anweisungen gekapselt sind und eine integrierte Funktion zur Überprüfung der Legitimität der Zustandsübergänge vorhanden

ist. Die Abbildung 2 soll einen Überblick über die Klassenstruktur, der State Machine liefern.


Abbildung 2 - Übersicht über das Klassendiagramm

Jeder Zustand ist in seiner eigenen Klasse definiert. Jede Klasse hat eine Enter-Methode,

die aufgerufen wird, wenn der Zustand betreten wird, eine Execute-Methode, die bei jedem

Aufruf von der State_Machine Klasse ausgeführt wird, und eine Exit-Methode, die aufgerufen

wird, wenn der Zustand verlassen wird. Um nicht jede Klasse einzeln aufrufen zu müssen,

nutzen wir das Prinzip der Polymorphie. Das bedeutet, wir behandeln Objekte verschiedener

Klassen, als wären sie vom gleichen Typ. Die spezifische Implementierung einer Methode

wird zur Laufzeit bestimmt. Hierzu haben wir eine Interface-Klasse mit den drei rein virtuellen

Methoden (Enter, Execute und Exit) erstellt. Diese Methoden sind im Compiler definiert, ihre

Implementierung erfolgt jedoch in den jeweiligen Zustandsklassen.

Die Zustandsmaschine basiert auf der selbst implementierten Klasse TState_Machine. Diese

Klasse beinhaltet zwei Templates: eines für die Spezialisierung der Zustandsmaschine und

eines für die Datenstruktur, die Daten zwischen den Zuständen austauscht.

Des Weiteren besitzt die Klasse zusätzliche Attribute wie currentState, welches den aktuellen

Zustand speichert, und m_pOwner, welcher als Zeiger auf die spezialisierten State Machine-

Instanzen dient. Die Klasse verfügt über Methoden wie Init, um einen Anfangszustand

festzulegen und m_pOwner eine Instanz zuzuweisen, ChangeState, um den Zustand zu

ändern und dabei die exit- und enter-Methoden aufzurufen, und Update, um die Execute-

Methode der aktuellen State-Klasse auszuführen.

In der Klasse State_Machine, die von TState_Machine erbt, werden nun die exakten

Parameter des Zustandsautomaten festgelegt. Dafür verfügt diese Klasse über Attribute, wie

Zeiger auf jede einzelne Zustandsklasse und eine Zustandstabelle. Der Konstruktor

State_Machine() erstellt neue Instanzen der einzelnen State-Klassen. Die Transition-

Methode ruft die ChangeState-Methode der TState_Machine Klasse auf und überprüft

anhand der Zustandstabelle, ob der Zustandsübergang legitim ist.

Darstellung eines Objektaufrufs

Anhand der folgenden Ausführungen soll beispielhaft die Steuerung einer Zustandsmaschine

mittels einer Instanz der Klasse State_Machine beschrieben werden.

Durch den Befehl State_Machine fsm; wird eine Instanz dieser Klasse erzeugt und der

Zustand der Maschine wird auf den im Konstruktor spezifizierten Anfangszustand gesetzt.

Der Wechsel von einem Zustand zu einem anderen erfolgt durch den Aufruf der Methode

Transition(transition). In Abbildung 3 wird die Abfolge dieses Zustandswechsels visualisiert.

Abbildung 3 - Illustration des Zustandswechsels

Die Methode leitet den Übergang von einem Zustand zum nächsten ein. Zunächst wird die

im Argumentwert übergebene Transition geprüft und bei Erfolg, die exit()-Methode des

aktuellen Zustands ausgeführt, woraufhin der Wechsel zum neuen Zustand stattfindet.

Anschließend wird die enter()-Methode des neuen Zustands aufgerufen.

Die Update()-Methode wird aufgerufen, um die spezifischen Logiken und Algorithmen, die in

jedem Zustand definiert sind, auszuführen. Abbildung 4 stellt diesen Prozess anhand des

Pre_Charge-Zustands dar, aber dieselbe Methode gilt auch für die anderen Zustände.

Abbildung 4 - Veranschaulichung der Ausführung der Execute-Methode

Zu Beginn des Prozesses wird das im currentState gespeicherte Objekt untersucht.

Abhängig vom dynamischen Typ des Objekts wird eine entsprechende Methode aufgerufen -

in diesem Beispiel handelt es sich um den Pre_Charge-Zustand. Innerhalb der Execute-

Methode wird dann die für den jeweiligen Zustand definierte Logik ausgeführt.

Erzeugung eines PWM-Ausgangssignals

Ein zentraler Bestandteil dieses Projekts war die Implementierung der sinusförmigen

Kommutierung für den Asynchronmotor. Zur Erzeugung der erforderlichen Pulsweiten-

modulation (PWM) wurde die SimpleFOC - Bibliothek verwendet, die einen Algorithmus für

die feldorientierte Steuerung bereitstellt. Für ein tiefergehendes Verständnis der Nutzung und

Funktionsweise dieser Bibliothek wird auf die zugehörige Dokumentation verwiesen, die

umfassende Erläuterungen zu den bereitgestellten Methoden und Funktionen bietet.

In diesem Projekt wurde die Open-Loop-Steuerung eingesetzt. Außerdem wird die

Dreiphasen-Halbbrücke mittels sechs separater PWM-Signale gesteuert. Die beiden

Methoden zur Erzeugung dieser Signale wurden in einem eigenen Namenspace zusammengefasst. Die Init()-Funktion innerhalb dieses Namensraums nimmt die

Initialisierung aller relevanten Motorparameter und Treiber vor.

Um den Motor zu steuern, wird die Methode move() verwendet. Sie nimmt ein Argument

namens new_target entgegen, welches die Winkelgeschwindigkeit repräsentiert, mit der der

Motor bewegt werden soll. Die Methode befindet sich in der selbst implementierten Funktion

PWM_Generation(BLDCMotor* motor, float freq), welche als Parameter einen Zeiger auf die

Instanz des Motorobjekts und eine Frequenz benötigt.

Verwendete Sensoren

Im Zuge des Projekts kamen sowohl der MAX31820 Temperatursensor als auch der

TLA2528 Analog-Digital-Wandler zum Einsatz.

Der MAX31820 ist ein digitaler Temperatursensor, der präzise Messungen ermöglicht und

über einen One-Wire-Bus gesteuert wird. Zur Steuerung dieses Sensors wurde die

DallasTemperature-Bibliothek verwendet, die eine Vielzahl an Methoden zur Vereinfachung

des Temperaturauslesens bereitstellt. Die dabei verwendeten Methoden wurden in der

Funktion readTemperature zusammengefasst.

Der TLA2528 wiederum ist ein 12-Bit-Analog-Digital-Wandler (ADC) mit acht Kanälen, der

über eine I2C-Schnittstelle gesteuert wird. Mithilfe des TLA2528 werden diverse Strom- und

Spannungsmessungen durchgeführt, die in Abbildung 5 dargestellt sind.


Abbildung 5 - Übersicht über die Aufgaben des TLA2528

Zu den durchgeführten Messungen zählen unter anderem die des Stroms in zwei Phasen,

wobei der Strom in der dritten Phase berechnet wird. Zudem wird der Eingangsstrom des

Stromnetzes erfasst. Des Weiteren überwacht der TLA2528 durch vier separate Messungen

die Spannung am Zwischenkreis, am Netz, die IGBT-Gate-Spannung sowie die

digitale Spannung.

Für den TLA2528 war keine vorgefertigte Bibliothek verfügbar, weshalb die notwendigen

Funktionen zur Steuerung des TLA2528 eigenständig entwickelt wurden.

Dies umfasst den Startprozess des ADCs, der das Einstellen eines Prescaler und das

Aktivieren eines Mittelwert-Filters für genauere Messergebnisse beinhaltet. Anschließend

erfolgt die interne Kalibrierung des Geräts, um mögliche Offset Fehler zu eliminieren. Nach

dem erfolgreichen Abschluss dieser Startsequenz ist der ADC bereit für die erste Messung.

Die Messung wird initiiert, indem die ID des auszulesenden Kanal über den I2C gesendet

wird. Anschließend wird ein Lesevorgang des Registers angefordert, in welches der ADC-

Wert nach der Messung gespeichert wird. Diese Vorgang startet den Messprozess und

schickt nach dessen Abschluss die Daten über den I2C Bus zurück.

Ausgabe über den Display

Bei der Darstellung aller relevanten Werte kommt ein 1,2-Zoll-Display zum Einsatz. Dieses

wird durch die Verwendung der Bibliotheken Adafruit_SSD1306.h und Adafruit_GFX.h

angesteuert. Dank vorhandener Dokumentationen zu diesen Bibliotheken können Nutzer

detaillierte Informationen über die verwendeten Methoden und Funktionen erhalten. Aus

diesem Grund wird in diesem Projektbericht nicht weiter darauf eingegangen.

Ausblick des Projekts

Das Software hat bereits wichtige Meilensteine erreicht, darunter die erfolgreiche

Implementierung der State Machine, die eine zentrale Rolle im Betrieb des Inverters spielt,

sowie die Feldorientierte Regelung (FOC) im Open-Loop-Modus mit der Unterstützung der

SimpleFOC-Bibliothek. Es ist jedoch zu beachten, dass es zu Kompatibilitätsproblemen

zwischen dieser Bibliothek und der verwendeten Hardware gekommen ist.

Blickt man auf die weitere Entwicklung des Projekts, stehen noch einige Aufgaben und Ziele

an. Eine herausragende Priorität ist dabei die Implementierung der Sensorlogik. Die korrekte

und effiziente Erfassung und Verarbeitung der Sensordaten ist von entscheidender

Bedeutung für die zuverlässige Funktion des Systems.

Ein | zusätzliches, | wünschenswertes | Feature | wäre | die | Implementierung | einer

temperaturgesteuerten Kühlung. Hier könnten Lüfter aktiviert werden, wenn die Temperatur

einen bestimmten Schwellenwert überschreitet. Dies würde nicht nur zur Zuverlässigkeit,

sondern auch zur Langlebigkeit des Systems beitragen.

Ein weiteres wichtiges Ziel ist die Implementierung der Safestate-Logik. Dafür müssen noch

diverse Fehlerfälle einprogrammiert werden, die den Safestate auslösen und ein

Mechanismus, um diesen wieder zurückzusetzen.

Außerdem muss noch der abschließende Test des Gesamtsystems stattfinden.

Weiterführende Links

Simple FOC

- https://docs.simplefoc.com/
- https://github.com/simplefoc

Dallas Temperature

- https://github.com/milesburton/Arduino-Temperature-Control-Library

TwoWire

- https://docs.arduino.cc/learn/communication/wire#wire-library

Adafruit Display

- https://github.com/adafruit/Adafruit_SSD1306

Github des Projekts

- https://github.com/Eg0st/MecProInverter

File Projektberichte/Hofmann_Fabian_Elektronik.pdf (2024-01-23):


# Mechatronik Projekt- Entwicklung und Herstellung eines Umrichters für Drehstrommaschinen

Fabian Hofmann: Mechanik – Thermische Belastung und Gehäuse

# Elektronik

## Inhalt

## 1.Abbildungsverzeichnis

## 2.Einführung

### Ziele

Ziel dieses Projektes war die Entwicklung und der Bau eines 3,6 kW Wechselrichters. Dieser sollte folgende Anforderungen erfüllen.

- Eingangsleistung von 3,6 kW (einphasig)
- Ausgang drei Phasen
- Ausgangs Frequenz variable von 10 bis 500 Hz
- Professionale Verarbeitung

Das gesamte Projekt wird Open Source sein, so dass Interessierte das Projekt replizieren können. Das Projekt ist in folgenden GitHub Repository vollständig einsehbar: https://github.com/Eg0st/MecProInverter

Da das Konzept einige Besonderheiten aufweist, sollte vor der Inbetriebnahme das Kapitel „Inbetriebnahme“ gelesen werden.

### Lösungsansatz

Der | Inverter | basiert | auf | einer | 3-Fach-Halbbrücke. | Dabei | wird | die
Wechselspannung zunächst über einen Brückengleichrichter gleichgerichtet und in den Zwischenkreiskondensatoren, hier mit C1 bezeichnet, geglättet. Anschließend wird aus der Gleisspannung mit der 3-Fach-Halbbrücke ein sinuskommutiertes PWM-Signal erzeugt. Wird dieses Signal auf einen Drehstrommotor gegeben, so erzeugt die große Induktivität in dem Motor einen Sinus aus der PWM.

Varistor; Vou t; GND; Voltage C onverter; ESP32; Vdd; Gate driver; screen; Multi Halfbridge; Poti; R2 LED1; R2 LED2; LED3; RGB WS2812; relais

Abbildung 1 Konzept Plan

Für die Steuerung sind weitere Komponenten wie z.B. ein Mikrocontroller erforderlich.

## 3.Konzepte

### GitHub Repository

Die kompletten Daten sind im GitHub Repository verfügbar. Hier befindet sich die komplette Elektronik in den Ordnern „MecProInverter\electronic“. Das KiCad Projekt befindet sich im Ordner „MecProInverter\electronic\MecProInverter“. Die verwendeten Bibliotheken befinden sich in den Ordnern own_library und JLC2KiCad_lib. Own_library enthält alle selbst erstellten Bibliotheken und JLC2KiCad enthält alle Bibliotheken, die über das Phython Skript JLC2KiCad erstellt wurden. Dieses Skript ermöglicht es von Komponenten von JLCPCB eine Bibliothek für KiCad herunterzuladen.

### Isolationskonzept

Um die Kosten niedrig zu halten, wurde beschlossen, die gesamte Elektronik bis auf wenige Ausnahmen nicht gegeneinander zu isolieren. Lediglich der USB-Anschluss und vier GPIO-Pins sind isoliert. Dies spart Kosten und Aufwand, ermöglicht aber trotzdem die Nutzung aller Funktionen. Daher muss das komplette Human-Interface gegen Berührung isoliert werden, um eine sichere Bedienung sicherzustellen. Das wird durch Plastik Verlängerungen der Taster etc. erreicht.

### Stromversorgung

Während des normalen Betriebes wird das ganze System über die Netzspannung versorgt. Jedoch werden für die Steuerung zwei Hilfsspannungen benötigt.

- 15 Volt
- 3,3 Volt

Aus der Netzspannung von 230 Volt werden mit Hilfe eines Fertigmoduls 15 Volt mit bis zu 1,2 Ampere erzeugt. Aus den 15 Volt werden mit einem DC/DC-Wandler 3,3 Volt erzeugt. Zusätzlich kann der 3,3 Volt Regler über den VBus des USB-Anschlusses versorgt werden.

### Auslegung Zwischen Kreis

Der Zwischenkreis wurde nachfolgender Formel ausgelegt. Es wurde mit einer Schaltfrequenz des IGBT von 10 kHz gerechnet.

C =

1
∆U

∗ I ∗ t

Daraus ergibt sich eine erforderliche Gesamtkapazität von 3 mF. Um Kosten zu sparen und den Platz besser zu nutzen, wurden drei 1 mF 325 Volt Kondensatoren parallelgeschaltet. Zur Sicherheit wurde der Einbauplatz für einen vierten vorbereitet.

## 4.Schaltplan

Der Schaltplan ist in zwei Teile gegliedert. Ein Teil enthält die gesamte Leistungselektronik und der zweite Teil enthält die Steuerung und Kommunikation. Dazu wurden in KiCad 7.0 zwei Pages erstellt. Die Power Page enthält die Leistungselektronik und die Controller Page den Rest. Im folgenden Kapitel wird auf alle Schaltungskomponenten eingegangen wobei der Schalplan im GitHub Repository zu finden ist. Die Datenblätter zu allen verwendeten Komponenten befinden sich im GitHub Ordner „GitHub\MecProInverter\electronic\datasheet“.

### Controller


Abbildung 2 Mikrocontroller-Schaltung

Als Controller kommt der ESP-S3 Mini zum Einsatz. Dieser bietet neben dem notwendigen MPWM-Modul auch eine direkte USB-Schnittstelle. Dadurch kann auf einen Serial to USB-Konverter verzichtet werden. Am Enabele Pin befindet sich ein Reset Taster, der über einen Pull Up Widerstand auf High gehalten wird. Dadurch kann der Controller bei Bedarf neu gestartet werden. Darunter befindet sich am GPIO-Pin 0 der Mood Taster. Solange dieser beim Start des Controllers gedrückt wird, startet dieser in den Bootmodus und kann programmiert werden.

### Steuerung

Der Wechselrichter ist mit
drei | Tastern | und | einem
Potentiometer zur Bedienung
ausgestattet. | Mit | dem
Potentiometer | kann | die
Frequenz eingestellt werden. Die drei Taster sind für die
restliche | Steuerung | und
Navigation im internen Menü
vorgesehen. | Im
Zusammenspiel | mit | dem
Display soll es möglich sein,
auch | detailliertere
Einstellungen vorzunehmen. Die Taster sind so beschaltet,
dass | sie | den | Pin | des
Controllers | auf | 3,3 | Volt
ziehen. Zusätzlich werden sie
über ein RC-Glied entprellt.


Dieses RC-Glied hat eine Einschaltverzögerung von 5 ms. Der Kondensator C50 sorgt dafür, dass die Spannung am Potentiometer geglättet wird.

### Anzeige


Abbildung 4 Anzeige-Schaltung

Der Inverter verfügt über ein Display und eine RGB-LED zur Statusanzeige etc. Die RGB-LED ist wie ein Schieberegister programmiert und kann über den DOUT mit weiteren LEDs verbunden werden. Zu beachten ist, dass der Betrieb der LED eine Versorgungsspannung von 3,5 Volt benötigt, es ist aber auch möglich, die LED mit 3,3 Volt zu betreiben. Für das Display wird ein I2C Display mit der Bezeichnung 938 der Firma Adafruit verwendet. Es handelt sich um ein 1“3 Zoll Oled Display.

Abbildung 3 Steuerungs-Schaltung

### Kommunikation


Abbildung 5 USB-C-Schaltung

Der Controller kann über eine isolierte USB-C-Buchse programmiert werden. Zusätzlich versorgt die USB-Schnittstelle über einen isolierten DC/DC-Wandler den 3,3 Volt Spannungswandler, so dass der Controller auch ohne zusätzliche Spannungsquelle betrieben und programmiert werden kann. Die isolierte USB-Schnittstelle bietet zudem den Vorteil, dass der Controller auch während des normalen Betriebs ausgelesen werden kann. Um einen Mindestschutz gegen ESD-Schäden zu gewährleisten, ist der USB-Eingang mit kurzangeschlossenen ESD-Dioden ausgestattet.


Neben | der | USB-
Schnittstelle verfügt der
Inverter | über | weitere
isolierte Datenein- und -
ausgänge. Darunter
befinden sich eine UART-Schnittstelle sowie zwei
freie GPIO-Pins. Da der
ESP-32 eine freie Wahl
der | PINs | für | die
Logikschnittstellen
bietet, | ist | es | somit
möglich, | an | diesen
beiden Pins eine isolierte I2C-Schnittstelle etc. zu
realisieren. | Diese
Schnittstelle | kann | für
eine externe Steuerung oder für einen externen Sensor verwendet werden. Eine weitere Anwendung wäre ein Not-Aus-Schalter.

Abbildung 6 Isolierte GPIO Pin Schaltung

### Lüfter Steuerung


Abbildung 7 Lüftersteuerung-Schaltung

Die beiden Lüfter zur Kühlung des Kühlkörpers sind parallelgeschaltet und können daher nur synchron geschaltet werden. Jeder hat jedoch einen eigenen PWM-Rückmeldeausgang. Damit kann sichergestellt werden, dass kein Lüfterfehler vorliegt. Die Ansteuerung der Lüfter sollte zunächst über ein PWM-Signal erfolgen, jedoch ist eine normale PWM-Ansteuerung bei den verwendeten Lüftern nicht möglich, da diese eine reine Gleichspannung zum Betrieb benötigen. Zu beachten ist auch, dass die Lüfter Highside geschaltet werden müssen, da sonst der PWM-Regelkreis nicht funktioniert. R31 ist für den Fall vorgesehen, dass die Versorgung der Lüfter mit mehr als 15 Volt zu Störungen führt. Die Spannung kann durch einen Vorwiderstand auf 12 Volt reduziert werden.

### Pree-Charge


Abbildung 8 PreeCharge-Schaltung

Die Vorladung dient zur Begrenzung des Einschaltstromes beim Einschalten des Gerätes. Ohne Pre-Charging werden die Zwischenkreiskondensatoren direkt an die Netzspannung angeschlossen, diese stellen im ersten Moment einen Kurzschluss dar, wodurch der maximal mögliche Strom abfällt. Im schlimmsten Fall kann der hohe Strom die interne Schaltung des Zwischenkreises beschädigen. Deshalb werden die Kondensatoren über einen Widerstand geladen. Sobald die Kondensatoren geladen sind, wird der Widerstand durch ein Relais überbrückt. Andernfalls würde unnötig Energie verschwendet. Das Relais ist normal offen und wird vom Mikrocontroller über einen Mosfet auf der Lowside geschaltet. Die Diode D4 wird benötigt, um mögliche Rückinduktionsströme, die beim Abschalten des Relais entstehen, kurzzuschließen. R18 wird als Vorwiderstand benötigt, da es sich bei dem Relais um ein handelsübliches und somit kostengünstiges 12-Volt-Relais handelt.

### Messungen


Abbildung 9 ADC und Hallsensor-Schaltung

Da der ESP32-S3 nur einen 12 Bit ADC mit großem Offset besitzt, wurde beschlossen, einen externen 8 Kanal ADC zu installieren. Dieser misst folgende Werte:

- Zwischenkreisspannung
- 3,3 Volt
- 15 Volt
- Eingangsstrom
- Ausgangstrom an der Phase U und W

Der ADC ist über I2C mit dem Mikrocontroller verbunden. Die Spannungsteiler für die Spannungsmessung sind so ausgelegt, dass sie bei Nennspannung eine Spannung von 2,5 Volt erzeugen. Außerdem besitzen sie alle einen Kondensator zur Spannungsglättung. Die Zwischenkreisspannung wird durch eine Diode und einen Kondensator gemessen. Der Widerstand R45 dient zur Entladung des Kondensators, um auch einen länger andauernden Spannungsabfall an der Zwischenkreisspannung messen zu können. Bei der Zwischenkreismessung wurden mehrere Widerstände in Reihe geschaltet, um die maximale Spannung der Widerstände nicht zu überschreiten.

Um den Strom auch auf der High Side messen zu können, werden Hallsensoren verwendet, die in Abhängigkeit vom Strom eine Spannung ausgeben. Da die verwendeten Sensoren einen Offset besitzen, kann mit ihnen auch ein negativer Strom gemessen werden. Diese Sensoren werden ebenfalls an den externen ADC angeschlossen. Mit dem Maschensatz kann der Strom der letzten Phase W genau berechnet werden.


Zur Messung der Kühlkörpertemperatur ist zusätzlich ein Steckplatz für einen One-Wire Temperatursensor vorbereitet. Dieser wird jedoch nicht benötigt, da das verwendete Powermodul über einen internen Temperatursensor verfügt.

### Stromversorgung

Für den Betrieb der Schaltung sind zwei Hilfsspannungen erforderlich. Zum einen 15 Volt für den Betrieb des IGBT, des Lüfters und des Relais. Zusätzlich werden 3,3 Volt für den Betrieb des Mikrocontrollers und der Peripherie benötigt. Aus den 230 Volt Wechselspannung werden also mit einem fertigen Modul 15 Volt erzeugt. Aus diesen werden dann über einen DC/DC-Wandler 3,3 Volt erzeugt. Zusätzlich ist es möglich, den 3,3 Volt DC/DC Wandler über die 5 Volt des USB-Anschlusses zu versorgen. Dazu wurden Dioden so eingebaut, dass sich die beiden Spannungsquellen nicht gegenseitig beeinflussen. J9 ist ein Messpunkt für.


Abbildung 10 Parallelschaltung Stromquellen-Schaltung


Abbildung 11 3,3 Volt Regler-Schaltung

Der Aufbau der 3,3 Volt DC/DC Wandler (TPS563201DDCR) ist dem Datenblatt entkommen. Die Spannung kann mithilfe der Widerstände R11 und R12 eingestellt werden.

### IGBT

Als Leistungsmodul kommt der IKCM20L60GA der Firma Infineon zum Einsatz. Dabei handelt es sich um eine Triple-H-Brücke mit integriertem Treiber. Dies hat den Vorteil, dass für den Betrieb nur eine minimale Anzahl von Bauteilen benötigt wird. Zusätzlich bietet das Modul die Möglichkeit, den aktuellen Betriebszustand bzw. die Temperatur über einen analogen Pin auszulesen. Zusätzlich kann über den ITRIP-Pin eine Strombegrenzung realisiert werden. Im Projekt wird der Pin direkt vom Mikrocontroller angesteuert, um das Modul im Fehlerfall abzuschalten.


Abbildung 12 IGBT-Schaltung

C1 bis C4 sind die Zwischenkreiskondensatoren und werden über das Netz auf ca. 325 Volt geladen. Die einzelnen MosFests werden über HINU, HINV, ... angesteuert. Diese haben eine Strombegrenzung, die mit Widerständen realisiert ist, um den Mikrocontroller zu schonen. C14 bis C19 dienen als Kondensator zur Erzeugung der Spannung zum Schalten der Highside Kondensatoren. Diese werden aufgeladen, wenn die Low Side Gates durchgeschaltet werden. Daher ist es nicht möglich, die High Side Gates von Anfang an durchzuschalten. Die weitere Schaltung ist dem Datenblatt bzw. der Application Note zu entnehmen.

## 5.Layout

Das Layout wurde in KiCad erstellt. Das Layout besteht aus 4 Ebenen. In der Darstellung ist die Oberseite rot und die Unterseite blau dargestellt. Die
Zwischenlängen | wurden | hauptsächlich | als | Grundriss | und | für | die
Spannungsversorgung verwendet. Die Spannungsversorgung ist hier jedoch je nach Bedarf in mehrere Bereiche unterteilt. Zusätzlich befindet sich in der rechten oberen Ecke ein Isolierbereich für isolierte Anschlüsse. Der Isolationsabstand zwischen den einzelnen Spannungsebenen beträgt 0,8 mm. Zu den isolierten Bereichen sind Abstände von 4 mm vorgesehen.


Abbildung 13 Layout (Ohne Zwischen Lagen)

Die | Platine | ist | so | aufgebaut, | dass | die | einzelnen | Komponenten | wie
Leistungselektronik, DC/DC-Wandler, Logikschaltungen möglichst getrennt sind.

Zu beachten ist auch, dass sich unterhalb der Antenne des ESP32-S3 keine Platine befinden darf, da dies die Performance des WLAN-Moduls beeinträchtigt. Für die mechanische Befestigung der Leistungsbauteile auf dem Kühlkörper sind zusätzliche Bohrungen vorgesehen. Die Aussparung auf der Oberseite dient als Kabeldurchführung für die Lüfter.

Es ist jedoch zu beachten, dass der Footprint des Brückengleichrichters nicht korrekt ist. Dieser ist seitenverkehrt und muss für eine V2 überarbeitet werden.

## 6. Inbetriebnahme

Die erste Inbetriebnahme ist durch Einstecken des USB-Steckers möglich. Dabei sollte bereits die 3,3 Volt LED aufleuchten. Außerdem sollte es möglich sein, den Micocontroller zu programmieren und die IOs anzusteuern.

Im nächsten Schritt kann über den 15 Volt Pin eine externe 15 Volt Spannungsquelle angeschlossen werden. Nun können die Lüfter, das Relais und der IGBT angesteuert werden und die 15 Volt LED sollte leuchten. Wird nun eine Spannung über den Zwischenkreis-Pin eingespeist, kann der IGBT am Ausgang getestet werden. Dabei ist zu beachten, dass zum Ansteuern der High-Treiber des IGBTs zunächst der Versorgungskondensator für die Treiber aufgeladen werden
muss. | Dies | geschieht, | sobald | die | Low-Treiber | der | einzelnen | Phasen
durchgeschaltet sind. Um den IGBT zu testen, ist es daher sinnvoll, ein PWM-Signal anzulegen. Um die Ausgänge des IGBT zu aktivieren, muss der ITRIP-Pin auf Low gesetzt werden.

Im letzten Schritt können 230 Volt angelegt werden. Dabei muss jedoch die 15 Volt Hilfsspannung abgeschaltet werden. Dabei ist zu beachten, dass der Vorladewiderstand ggf. über den Kühlkörper gekühlt oder anderweitig überbrückt
werden | muss. | Alternativ | kann | die Spannung durch einen | regelbaren
Trenntransformator etc. langsam erhöht werden.

Da der USB-Anschluss isoliert ist kann bei jedem Schritt der Status des Inverters über den Micocontroller überwacht werden.

## 7.Tests

Alle Komponenten mit einer Versorgungsspannung von bis zu 15 Volt wurden auf Funktion getestet. Alles funktionierte wie erwartet und sind deshalb nicht interessant. Daher wird in diesem Kapitel nur Versuche dokumentiert, die bei höheren Spannungen durchgeführt wurden. Es wurden folgende zwei Versuche durchgeführt.

### Versorgung über 230 Volt an einem Trenntransformator

Der Wechselrichter wurde an den Trenntransformator angeschlossen und die Spannung langsam erhöht. Damit sollte sichergestellt werden, dass die Spannungsversorgung funktioniert und kein Kurzschluss vorliegt. Dazu wurde die Zwischenkreisspannung extern mit einem Multimeter gemessen.

Es ist zu beobachten, dass die Spannung am Zwischenkreis mit steigender Eingangsspannung zunimmt. Wobei diese um einen Faktor von ca. 1,4 höher ist. Dies ist auf die Gleichrichtung der Wechselspannung zurückzuführen. Ab einer Spannung von ca. 100 Volt schaltet der 15 Volt und 3,3 Volt Spannungskreis. Eine
weitere | Erhöhung | der | Spannung | führt | nur | zu | einer | Änderung | der
Zwischenkreisspannung.

### Ansteuerung des IGBT bei 100 V mit PWM-Sinuskommutierung

In diesem Versuch soll die PWM-Sinuskommutierung am Ausgang des IGBT überprüft werden. Dazu wird der Wechselrichter über einen Trenntrafo mit Spannung versorgt. Die Spannung wird so gewählt, dass alle Komponenten funktionieren (15 Volt Regler). Nun wird mit Hilfe eines Oszilloskops der unbelastete Ausgang des Wechselrichters betrachtet. Dabei wurden die einzelnen Phasen es Ausgangs gegen Masse dargestellt.

Die folgenden Spannungsverläufe wurden zu verschiedenen Zeitpunkten aufgezeichnet. Am Zwischenkeil wurde eine Spannung von 100 Volt gemessen.


Abbildung 14 Testergebnis Einschaltdauer ca. 20

Es ist gut zu erkennen, dass der IGBT bis zu den 100 Volt des Zwischenkreises voll durchschaltet und auch gegen Masse schaltet.


Abbildung 15 Testergebnis Einschaltdauer ca. 80

Dieser Abschnitt wurde zu einem späteren Zeitpunkt hinzugefügt. Durch die Änderung der Steuerzeiten ist anzunehmen, dass die PWM-Sinuskommutierung funktioniert.

Abbildung 16 Testergebnis Duty Cycle sweep

Diese Abbildung zeigt eine Überlagerung über einen längeren Zeitraum. Es ist gut zu erkennen, dass die PWM über den gesamten Zeitraum variiert.

Diese Ergebnisse zeigen, dass der Betrieb auf einem Motor sicher funktioniert. Aus Zeitgründen konnte dieser Versuch jedoch nicht durchgeführt werden.

## 8.Ausblick

Derzeit befindet sich der Wechselrichter in einem nicht vollständig getesteten Zustand. Außerdem enthält das Layout einen Fehler im Footprint des Brückengleichrichters (siehe Kapitel Schaltplan). Die Versuche lassen erwarten, dass der Betrieb des Motors keine Probleme bereitet.

Sollte das Projekt weiterentwickelt werden, wird empfohlen, eine zweite Version der Platine zu erstellen, die einen deutlich kompakteren 15-Volt Regler besitzt. Dies ermöglicht auch eine Vergrößerung der Isolationsabstände. Außerdem sollte eine automatische Entladung der Zwischenkreiskondensatoren realisiert werden, da dieser bis zu 5 Minuten zum Entladen benötigt, was ein gewisses Risiko darstellt. Auch eine Überarbeitung der Anschlussklemmen mit größeren Phasenabständen etc. kann zur Verbesserung der Sicherheit beitragen. Eine weitere Überlegung ist die Erhöhung der Leistung durch Umstellung der Stromversorgung auf Drehstrom.

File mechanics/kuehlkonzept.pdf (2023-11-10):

# Main Power Losses in MECPRO-Inverter

RtℎK =; − (RtℎG + RtℎM); Bridge rectifier; = (RtℎG − RtℎM)

Thermal resistance of Heat Sink (Fischer electronics)

θi = Maximum Junction Temperature

θu = Ambient Temperature

RtℎG = Tℎermal Resistance of Semiconductor

RtℎM = Tℎermal Resistance of Mounting Area

- Maximum Operating Temperature Tjmax = 150°C = θi
- Thermal resistance without heat sink R0JA = 24 °C

- Thermal resistance with heat sink R0JC = 1
- Power dissipation Ptot(@Dutycycle = 0,8 − 1 &@10A) ≅ 8 W − 10 W

Heat Sink Requirements
Compensation Temperature and Thermal Resistance of Heat Sink:

TBR = R0JA ∗ Ptot =

1K
W

∗ 10 W = 10K = θi

RtℎK =

TBR

Ptot

− R0JC =

10K
8W

−

1K
W

=

0,25K
W

Outer Dimensions
Cooling Area
ACBR = (30 ± 0,3 ∗ 20 ± 0,3)mm²

CIPOS
- Maximum Operating Temperature Tmax = 125°C = θi
- Thermal resistance Single IGBT RTH1 = 4,28 K
W
- Thermal resistance Single Diode RTH2 = 4,87 K
W
- Power dissipation Ptot(per IGBT) = 29,2 W


Heat Sink Requirements

TCiPOS = (RTH1 + RTH2

) ∗ Ptot =

(4,28 + 4,87)K
W

∗ 29,2W = 267,18K

Compensation Temperature and Thermal Resistance of Heat Sink:

∆TCIPOS = TCIPOS − (θi − 25K) = 267,18K − 100K = 167,18K

⇒ RtℎK =

∆TCIPOS

Ptot

− (RTH1 + RTH2

) =

167,18K
29,2W

−

4,87 ∗ 4,28K
(4,87 + 4,28)W

=

3,467K
W

Outer Dimensions
Cooling Area:
ACCIPOS = (33,8 ± 0,3 × 21 ± 0,3)mm²

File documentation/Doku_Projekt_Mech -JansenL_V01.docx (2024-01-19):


# Mechatronik Projekt- Entwicklung und Herstellung eines Umrichters für Drehstrommaschinen

Lukas Jansen: Mechanik – Thermische Belastung und Gehäuse

# Konzeptphase

Während der Konzeptphase sind einige Grundlagen festzulegen. Ein erstes logisches Schaltbild kann erstellt werden. So ist die Gesamtaufgabe in Einzelaufgaben zu unterteilen.

Abbildung 1: Erster logischer Schaltungsentwurf, ohne genaue Bauteilangaben, jedoch nach prinzipiell richtigem Aufbau

So erhält man einen ersten Überblick über die einzelnen Bauteile und notwendige Modifikationen können nach dem ersten Ansatz bereits durchgeführt werden. Die Aufgabe ist es, einen Umrichter zu entwickeln, der zunächst die 230V Netzspannung über Gleichrichter in eine 15V Gleichspannung wandelt und diese dann mittels Halbbrücken IGBTs in eine dreiphasige Wechselspannung wandelt. Die Leistungsanforderungen an den Umrichter sind 3,6KW. Der Einsatzbereich liegt in der Kategorie für kleine bis mittlere Zerspanungsmaschinen.

# Thermische Eigenschaften

In diesem Abschnitt sollen die Thermischen Eigenschaften des Umrichters festgelegt werden. Unter diesen Bereich fällt in erster Linie das Kühlkonzept. Zunächst ist eine maximal zulässige Gehäuse-Temperatur vorzugeben. Da das Gehäuse in der Regel berührbar ist, wird hier eine Maximaltemperatur von 60°C gewählt, um Verletzungen durch Verbrennung vorzubeugen. Das ergibt bei typischer Umgebungstemperatur (Raumtemperatur =20°C) einen erlaubten Temperaturhub von 40°C oder 40K. Mit dem vorgegebenen Bauraum sind somit die Anforderungen an das Kühlkonzept weitestgehend definiert.

Um die Anforderungsliste noch genauer zu spezifizieren ist die Wärmeleistung der eingesetzten Bauelemente zu ermitteln. Die kritischen Bauteile sind dabei die Umrichter-IGBTs und die Gleichrichter-Dioden. Nach der Bauteilauswahl kann aus der Spezifikation der Bauteile die zu kompensierende Leistung ermittelt werden.

## Gleichrichter

Die Spezifikation des Brückengleichrichters gibt folgende Leistungsverluste an.


Abbildung 2: Brückengleichrichter – Leistungsverluste bei Vorwärtsbetrieb mit gegebenem Dutycycle [1]

Die Verlustleistung ist ablesbar für einen Duty-Cycle von 0,8 – 1 bei 10A Stromverbrauch. Der Leistungsverlust beträgt 8– 10 Watt. Im Folgenden sind 10 Watt Verlustleistung im Brückengleichrichter angenommen. Diese Leistung wird in Wärme umgewandelt.

## IGBT-Baustein (IKCM20L60GA)

Die Ausgangsspannung wird von einem IGBT-Baustein bestehend aus 6 Halbbrücken-IGBTs und einem integrierten Brückentreiber zur Verfügung gestellt. Die in Wärme umgesetzte Leistung ergibt sich aus der Spezifikation des Bausteins.


Abbildung 3: Dynamische Parameter des IGBT-Bausteins. [2]

Abbildung 3 stellt die Schaltparameter des IGBT-Bausteins dar. Markiert sind die Schaltenergien, die zur Erwärmung beitragen. Zusätzlich müssen die statischen Parameter betrachtet werden.


Abbildung 4: Statische Parameter des IGBT-Bausteins – Auszug [2]

Abbildung 4 zeigt die statischen Parameter des Bausteins. Hier ist die Dioden-Vorwärtsspannung und der Vorwärtsstrom von Interesse. Der relevante Bereich ist markiert. Es wird der Typische Wert bei 25°C angenommen.

Nachfolgende Tabelle 1 stellt die Berechnungsgrundlagen für die Wärmeverluste übersichtlich zusammen.

I_(FW) Strom im Vorwärtsbetrieb | 16 | A/(Phase)
V_F Spannungsabfall im Vorwärtsbetrieb | 1,7 | V
P_V =16A*1,7V Verlustleistung im Vorwärtsbetrieb pro Phase | 27,2 | W/(Phase)
P_(tot01) Verlustleistung Aktiv Vorwärtsbetrieb | 81,6 | W
IGBT_(Eoff) Energieverluste beim Abschalten | 270 | μJ
IGBT_(Eon) Energieverluste beim Einschalten | 470 | μJ
F_(PWM) Schaltfrequenz im Normalbetrieb | 10 | KHz
P_(SW) =(IGBT_(Eoff) +IGBT_(Eon) )*F_(PWM) Verlustleistung durch Umschaltvorgägne | 22,2 | W
P_(tot) =P_(tot01) +P_(SW) Verlustleistung Gesamt | 103,8 | W
P_(SF) ≈(P_(tot) +P_(tot) +P_(BRGR) )*1,1 Verlustleistung mit Sicherheitsfaktor von 10% | 120 | W

Tabelle 1: Verlustleistung durch IGBTs. Werte entstammen dem Datenblatt für die IGBTs von Infineon Technologies

Es ergibt sich eine Verlustleistung von 120 Watt. Unter der Annahme, dass diese Leistung vollständig in Wärme umgewandelt wird, und die Gesamttemperatur des Geräts 60°C nicht überschreiten soll, stehen die Anforderungen an den Kühlkörper fest.

R_(thK) =(60°C-20°C)/(120W)=0,33K/W

## Kühlkörper

Die Auslegung des Kühlkörpers kann in zwei Bereiche geteilt werden. Aktive und passive Kühlung. Zunächst wird versucht eine passive Kühlung einzusetzen. Es kommen unterschiedliche Bauweisen von Kühlkörpern in Frage.


Abbildung 5: Profile ähnlicher Kühlkörper und deren Thermischer Widerstand über der Länge [3] , [4]

Die gezeigten Kühlköper in Abbildung 5 erfüllen die Anforderungen an den gewünschten thermischen Widerstand nicht vollständig. Jedoch passen sie zu den Abmessungen der Leiterplatte mit 120x150mm². Ein weiterer Kühlkörper aus dem Materialvorrat des Labors für Leistungselektronik mit ähnlichen Abmessungen wird verwendet. Es wird dabei der gleiche thermische Widerstand von 0,5K/W angenommen. Da dies nicht ausreichend ist um die Erwärmung des Gesamtbauteils um 40K zu beschränken, ist es notwendig aktiv zu kühlen.

Abbildung 6: Anpassung des thermischen Widerstandes mit forcierter Kühlung [5]

Abbildung 6 zeigt den Zusammenhang zwischen dem Wärmewiderstand aus natürlicher Kühlung und dem Wärmewiderstand durch forcierte Kühlung. Rechts neben dem mathematischen Zusammenhang ist der Proportionalitätsfaktor Alpha über der Windgeschwindigkeit für forcierte Kühlung dargestellt.

Es gilt:

R_(thK) =0,5 und R_(thKf) =0,33 ⟹ α=(0,33)/(0,5)=0,6 ⟹v_(Wind) =1,2m/s

Damit ist kann der Lüfter ausgewählt werden. Bei den meisten Lüftern ist in der Regel der Volumenstrom in Kubikmeter pro Stunde angegeben. Über die Oberfläche des Lüfters und Umrechnung in Meter Pro Sekunde ergibt sich eine Geschwindigkeit, bei der ein Abschlag von 40% durchgeführt wird, aufgrund der später noch angebrachten Schutzkappe.

Berechnung

Das Thema thermische Eigenschaften ist somit ausreichend berücksichtigt.

# Konstruktion

Der Frequenzumrichter besteht im Grunde aus vier Einzelteilen, den Lüftern, dem Kühlkörper, der Leiterplatte und einer Abdeckung. Da die Leiterplatte durch den Leiterplattenentwurf fest vorgegebene Geometrien verfügt, beschränkt sich die Konstruktion auf die Abdeckung, die Nachbearbeitung des Kühlkörpers und eine Aufnahme, sowie eine Schutzkappe für die Ventilatoren.

## Nachbearbeitung Kühlkörper

Der Kühlkörper muss auf die Leiterplatte zugeschnitten werden. Er hat eine Erdungs- und Gehäuse-Trägerfunktion. Der Kühlkörper schützt die Leiterplatte vor Verbiegen. Stoßsicherheit ist durch den Kühlkörper nicht gegeben.


Abbildung 7: Fertigungsorientierte Zeichnung des Kühlkörpers mit Schnittdarstellung in der unteren linken Ecke.

Der Kühlkörper dient des Weiteren als festes Grundelement. Hier werden alle Schrauben befestigt. Löcher für die Kondensatoren auf der Leiterplatte sind ebenfalls notwendig. Abbildung 7 zeigt die Zeichnung zum Fräsen besagter Löcher. In diesem Fall wurde auf fertigungsnahe Bemaßung geachtet.

- Fertigung

## Abdeckung

Die Abdeckung dient in erster Linie als Berührschutz. Leichte Verschmutzungen können abgehalten werden. Gegen Spritzwasser ist das Gehäuse nicht sicher. Stöße durch spitze und harte Gegenstände können von der Schutzkappe nur bedingt abgehalten werden. Die Schutzkappe darf mit konstanten bzw. schwellenden Zug- oder Druckkräfte belastet werden.

- Bild
- Simulation
- Fertigung

## Aufnahme und Abdeckung des Lüfters

- Fertigung
- Bild
- Beschreibung


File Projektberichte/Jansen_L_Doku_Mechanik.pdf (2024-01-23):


# Mechatronik Projekt-Entwicklung und Herstellung eines Umrichters für Drehstrommaschinen

Lukas Jansen: Mechanik – Thermische Belastung und Gehäuse

## Inhalt

## Konzeptphase

Während der Konzeptphase sind einige Grundlagen festzulegen. Ein erstes logisches Schaltbild kann erstellt werden. So ist die Gesamtaufgabe in

Einzelaufgaben zu unterteilen.; Varistor; Vou t; GND; Voltage C onverter; ESP32; Vdd; Gate driver; screen; Multi Halfbridge; Poti; R2 LED1; R2 LED2; LED3; RGB WS2812; relais

Abbildung 1: Erster logischer Schaltungsentwurf, ohne genauere Bauteilangaben.

So erhält man einen ersten Überblick über die einzelnen Bauteile und notwendige Modifikationen können nach dem ersten Ansatz bereits durchgeführt werden. Die Aufgabe ist es, einen Umrichter zu entwickeln, der zunächst die 230V Netzspannung über Gleichrichter in eine 15V Gleichspannung wandelt und diese dann mittels Halbbrücken IGBTs in eine dreiphasige Wechselspannung wandelt. Die Leistungsanforderungen an den Umrichter sind 3,6KW. Der Einsatzbereich liegt in der Kategorie für kleine bis mittlere Zerspanungsmaschinen.

## Thermische Eigenschaften

In diesem Abschnitt sollen die Thermischen Eigenschaften des Umrichters festgelegt werden. Unter diesen Bereich fällt in erster Linie das Kühlkonzept. Zunächst ist eine maximal zulässige Gehäuse-Temperatur vorzugeben. Da das Gehäuse in der Regel berührbar ist, wird hier eine Maximaltemperatur von 60°C gewählt, um Verletzungen durch Verbrennung vorzubeugen. Das ergibt bei typischer Umgebungstemperatur (Raumtemperatur =20°C) einen erlaubten Temperaturhub von 40°C oder 40K. Mit dem vorgegebenen Bauraum sind somit die Anforderungen an das Kühlkonzept weitestgehend definiert.

Um die Anforderungsliste noch genauer zu spezifizieren ist die Wärmeleistung der eingesetzten Bauelemente zu ermitteln. Die kritischen Bauteile sind dabei die Umrichter-IGBTs und die Gleichrichter-Dioden. Nach der Bauteilauswahl kann aus der Spezifikation der Bauteile die zu kompensierende Leistung ermittelt werden.

### Gleichrichter

Die Spezifikation des Brückengleichrichters gibt folgende Leistungsverluste an.


Abbildung 2: Brückengleichrichter – Leistungsverluste bei Vorwärtsbetrieb mit gegebenem Dutycycle [1]

Die Verlustleistung ist ablesbar für einen Duty-Cycle von 0,8 – 1 bei 10A Stromverbrauch. Der Leistungsverlust beträgt 8– 10 Watt. Im Folgenden sind 10 Watt Verlustleistung im Brückengleichrichter angenommen. Diese Leistung wird in Wärme umgewandelt.

### IGBT-Baustein (IKCM20L60GA)

Die Ausgangsspannung wird von einem IGBT-Baustein bestehend aus 6 Halbbrücken-IGBTs und einem integrierten Brückentreiber zur Verfügung gestellt. Die in Wärme umgesetzte Leistung ergibt sich aus der Spezifikation des Bausteins.

Abbildung 3: Dynamische Parameter des IGBT-Bausteins. [2]

Abbildung 3 stellt die Schaltparameter des IGBT-Bausteins dar. Markiert sind die Schaltenergien, die zur Erwärmung beitragen. Zusätzlich müssen die statischen Parameter betrachtet werden.


Abbildung 4: Statische Parameter des IGBT-Bausteins – Auszug [2]

Abbildung 4 zeigt die statischen Parameter des Bausteins. Hier ist die Dioden-Vorwärtsspannung und der Vorwärtsstrom von Interesse. Der relevante Bereich ist markiert. Es wird der Typische Wert bei 25°C angenommen.

Tabelle 1 stellt die Berechnungsgrundlagen für die Wärmeverluste übersichtlich zusammen.

IFW Strom im Vorwärtsbetrieb | 16 | A Pℎase
VF Spannungsabfall im Vorwärtsbetrieb | 1,7 | V
PV = 16A ∗ 1,7V Verlustleistung im Vorwärtsbetrieb pro Phase | 27,2 | W Pℎase
Ptot01 Verlustleistung Aktiv Vorwärtsbetrieb | 81,6 | W
IGBTEoff Energieverluste beim Abschalten | 270 | μJ
IGBTEon Energieverluste beim Einschalten | 470 | μJ
FPWM Schaltfrequenz im Normalbetrieb | 10 | KHz
PSW = (IGBTEoff + IGBTEon) ∗ FPWM Verlustleistung durch Umschaltvorgägne | 22,2 | W
Ptot = Ptot01 + PSW Verlustleistung Gesamt | 103, 8 | W
PSF ≈ (Ptot + Ptot + PBRGR) ∗ 1,1 Verlustleistung mit Sicherheitsfaktor von 10% | 120 | W

Tabelle 1: Verlustleistung durch IGBTs. Werte entstammen dem Datenblatt für die IGBTs von Infineon Technologies

Es ergibt sich eine Verlustleistung von 120 Watt. Unter der Annahme, dass diese Leistung vollständig in Wärme umgewandelt wird, und die Gesamttemperatur des Geräts 60°C nicht überschreiten soll, stehen die Anforderungen an den Kühlkörper fest.

RtℎK =

60°C − 20°C
120W

= 0,33

K
W

### Kühlkörper

Die Auslegung des Kühlkörpers kann in zwei Bereiche geteilt werden. Aktive und passive Kühlung. Zunächst wird versucht eine passive Kühlung einzusetzen. Es kommen unterschiedliche Bauweisen von Kühlkörpern in Frage.


Abbildung 5: Profile ähnlicher Kühlkörper und deren Thermischer Widerstand über der Länge [3] , [4]

Die gezeigten Kühlköper in Abbildung 5 erfüllen die Anforderungen an den gewünschten thermischen Widerstand nicht vollständig. Jedoch passen sie zu den Abmessungen der Leiterplatte mit 120x150mm². Ein weiterer Kühlkörper aus dem Materialvorrat des Labors für Leistungselektronik mit ähnlichen Abmessungen wird verwendet. Es wird dabei der gleiche thermische Widerstand von 0,5K/W angenommen. Da dies nicht ausreichend ist um die Erwärmung des Gesamtbauteils um 40K zu beschränken, ist es notwendig aktiv zu kühlen.


Abbildung 6: Anpassung des thermischen Widerstandes mit forcierter Kühlung [5]

Abbildung 6 zeigt den Zusammenhang zwischen dem Wärmewiderstand aus natürlicher Kühlung und dem Wärmewiderstand durch forcierte Kühlung. Rechts neben dem mathematischen Zusammenhang ist der Proportionalitätsfaktor Alpha über der Windgeschwindigkeit für forcierte Kühlung dargestellt.

Es gilt:

RtℎK = 0,5 und RtℎKf = 0,33 ⟹ α =

0,33
0,5

= 0,6 ⟹ vWind = 1,2

m
s

Damit ist kann der Lüfter ausgewählt werden. Bei den meisten Lüftern ist in der Regel der Volumenstrom in Kubikmeter pro Stunde angegeben. Über die Oberfläche des Lüfters und Umrechnung in Meter Pro Sekunde ergibt sich eine Geschwindigkeit, bei der ein Abschlag von 20% durchgeführt wird, aufgrund der später noch angebrachten Schutzkappe.

Vwind =

Volumenstrom
Lüfteroberfläcℎe

∗ 0,8 =

18

m³
ℎ
0,0025m² ∗ 3600s

∗ 0,8 = 1,6

m
s

Der Ausgewählte Lüfter hat eine Oberfläche (konservativ geschätzt) eine Oberfläche von 50x50mm². Man könnte hier auch eine radiale Oberfläche für den Luftstrom ansetzen. Dies würde die Windgeschwindigkeit jedoch noch weiter erhöhen, da die radiale Fläche, die von den Rotorblättern des Lüfters abgedeckt wird kleiner ist als die Außenmaße des Lüfters.

Das Thema thermische Eigenschaften ist somit ausreichend berücksichtigt.

## Konstruktion

Der Frequenzumrichter besteht im Grunde aus vier Einzelteilen, den Lüftern, dem Kühlkörper, der Leiterplatte und einer Abdeckung. Da die Leiterplatte durch den Leiterplattenentwurf fest vorgegebene Geometrien verfügt, beschränkt sich die Konstruktion auf die Abdeckung, die Nachbearbeitung des Kühlkörpers und eine Aufnahme, sowie eine Schutzkappe für die Ventilatoren.

### Nachbearbeitung Kühlkörper

Der Kühlkörper muss auf die Leiterplatte zugeschnitten werden. Er hat eine Erdungs- und Gehäuse-Trägerfunktion. Der Kühlkörper schützt die Leiterplatte vor Verbiegen. Stoßsicherheit ist durch den Kühlkörper nicht gegeben.


Abbildung 7: Fertigungsorientierte Zeichnung des Kühlkörpers mit Schnittdarstellung in der unteren linken Ecke.

Der Kühlkörper dient des Weiteren als festes Grundelement. Hier werden alle Schrauben befestigt. Löcher für die Kondensatoren auf der Leiterplatte sind ebenfalls notwendig. Abbildung 7 zeigt die Zeichnung zum Fräsen besagter Löcher. In diesem Fall wurde auf fertigungsnahe Bemaßung geachtet.

Die Bearbeitung des Kühlkörpers erfolgte mit Kappsäge, CNC-Fräsmaschine und Standbohrmaschine. Die Schraubenlöcher sind als M3 Standardgewinde ausgeführt.

### Abdeckung

Die Abdeckung dient in erster Linie als Berührschutz. Leichte Verschmutzungen können abgehalten werden. Gegen Spritzwasser ist das Gehäuse nicht sicher. Stöße durch spitze und harte Gegenstände können von der Schutzkappe nur bedingt abgehalten werden. Die Schutzkappe darf mit konstanten bzw. schwellenden Zug- oder Druckkräften belastet werden.


Abbildung 8: Abdeckung der Leiterplatte mit Schraubenlöchern zur Durchsteckmontage und Aussparungen für sämtliche Elemente der Mensch-Maschine-/ Maschine-Maschine Schnittstelle

Wie Abbildung 8 erkennbar, ist die Abdeckung mit Aussparungen für USB-C Schnittstelle, Anschlussklemmen, Taster und Potentiometer, sowie einem Fenster für den Bildschirm und die RGB-LED zur Statusanzeige versehen. An dieser Stelle könnte eine Simulation für mechanische Belastungsfähigkeit erstellt behandelt werden.

- Simulation

Als Fertigungsverfahren kam das FDM-3D-Druckverfahren zum Einsatz. Hier ist es zweckmäßig 100% Materialausfüllung einzustellen, um eventuell spätere Änderungen (zb. Weitung der Bohrungen und Ausschnitte) zu ermöglichen. Dennoch ist es wichtig, Spieltoleranzen einzuräumen. Hier wurde der Lochdurchmesser auf -0,2mm ausgeführt, während die Aussparungen für die Anschlüsse ebenso auf -0,2mm konstruiert sind.

### Aufnahme und Abdeckung des Lüfters

Die Aufnahme des Lüfters ist als Klammer ausgeführt, die den Lüfter umgreift und mit M3 Schrauben befestigt ist.


Abbildung 9: Explosionsdarstellung des montierten Lüfters und seiner Aufnahme

Ein wichtiges Detail zeigt Abbildung 9. Um den Platzbedarf zu reduzieren wurden die Schrauben, die die Klammer am Kühlkörper befestigen (1) versenkt ausgeführt, um die kreuzende Schraube, die den Lüfter mit der Klammer verbindet (2) darüber kreuzt. Des Weiteren ist eine Aussparung zur erleichterten Montage der senkrechten Schraube (1) vorgesehen. Die Abdeckung des Lüfters kann über die waagrechten Schrauben (2) und (3) an den Klammern befestigt werden. Die Abdeckung ist notwendig, um den Lüfter vor grober Verschmutzung zu schützen.


Abbildung 10: Abdeckung des Lüfters mit Polygonmuster für die Luftzufuhr.

Abbildung 10 veranschaulicht die Ausführung der Abdeckung des Lüfters. Ein Polygonmuster ermöglicht den Luftstrom und soll gleichzeitig größere

Verschmutzungen vermeiden. Schraubenlöcher für die Montage sind ebenfalls als M3 Durchsteckmontage vorgesehen. Gefertigt wurden beide Bauteile mit dem FDM-3D-Druckverfahen.

### Taster

Da die Taster auf der Leiterplatte unter der Abdeckung verborgen sind, müssen Verlängerungen für die Taster entworfen werden. In der Abdeckung wird eine Führung für den Taster eingebaut. Die Verlängerung selbst wurde mit einer Druckfeder versehen, um die Verlängerung in Position zu halten. Gefertigt wurden die Taster mit FDM-Druckverfahren. Hier ist zu erwähnen, dass der FDM-Druck nicht für diese Dimensionen geeignet ist. Die Fertigung der Taster ist nicht gelungen. Ein alternatives Druckverfahren wäre das SLA-Druckverfahren, bei dem eine höhere Auflösung und somit besser Genauigkeit und kleinere Bauteile gefertigt werden können. Die Materialeigenschaften und Dimensionen der Druckfeder sind in folgender Tabelle aufgelistet.

Minimale Arbeitslänge | LW = 7,5 | mm
Federkonstante | c = 0,06 | N mm
Außendurcℎmesser | d = 3,45 | mm
Draℎtdurcℎmesser | b = 0,25 | mm


Abbildung 11: Taster, als Einzeldarstellung links und rechts im Gehäuse eingebaut als Schnittdarstellung

Das Taster-Design ist in Abbildung 11 dargestellt. Auf der linken Seite ist ein einzelner Taster zu erkennen. Rot markiert ist der Absatz, auf dem die Druckfeder sitzt. Rechts ist eine Schnittdarstellung der Taster im Gehäuse zu erkennen. Unten in grüner Farbe sichtbar ist die Leiterplatte. Die eigentlichen Taster sind in rot dargestellt und darüber befindet sich die Verlängerung der Taster (schwarz) mit Führung (weiß) und Druckfeder (metallic).

### Endmontage

Das Finale Ergebnis der Konstruktion ist in Abbildung 12 links und als Explosionszeichnung (rechts) dargestellt. Bei der Endmontage traten aufgrund von Fertigungstoleranzen Probleme auf. Die Abdeckung musste nachbearbeitet werden (geschliffen). Zusätzlich erwiesen sich zwei Bohrungen am Kühlkörper als Fehlerhaft. Acht Bohrungen mussten mit Hand gefertigt werden. Dabei kam es zu größeren Messungenauigkeiten beim Anreißen. Als Anreißwerkzeug wurde ein Messschieber verwendet, dessen Messbereich kleiner war als der Abstand der Bohrungen zur Bemaßungskante. Es musste eine zweite Bemaßungskante verwendet werden. Somit addieren sich die Toleranzen für die Länge des Kühlkörpers und die der Bohrungen. Im Endergebnis sind die Schraubenlöcher um etwa 200 Micrometer gegenüber den Durchstecklöchern auf der Abdeckung versetzt. Die Schrauben am vorderen Ende des Umrichters konnten deshalb nicht montiert werden.


Abbildung 12: Montiertes Gehäuse, links und Explosionszeichnung rechts

## Fazit

Das Gehäuse besteht aus den Einzelteilen Kühlkörper, Abdeckung, Lüfter – Gehäuse und Aufnahme. Weitere Kleinteile wie Taster Verlängerung und Potentiometer Verlängerung waren ebenfalls zu entwerfen. Grundsätzlich ist das FDM-3D Druckverfahren ein gut geeignetes Fertigungsverfahren, besonders wenn es um schnelle Prototypenfertigung geht. Es bringt jedoch Einschränkungen in Größe der zu fertigenden Bauteile mit sich. Ein wichtiges Element in der Entwicklung eines Technischen Geräts ist die Projektplanung. Speziell im Bezug auf die Taster, hätte der Einsatz eines anderen Fertigungsverfahrens womöglich eine Lösung darstellen können. Dazu wäre es nötig gewesen, erste Testdrucks bereits in einer früheren Projektphase anzufertigen. Im Bezug auf die Mechanischen Bauteile wäre es zweckdienlicher gewesen, kleinere und genauer spezifizierte Meilensteine zu festzulegen und deren Einhaltung stärker zu verfolgen.

Abbildung 1: Erster logischer Schaltungsentwurf, ohne genaue Bauteilangaben,
jedoch nach prinzipiell richtigem Aufbau | 2
Abbildung 2: Brückengleichrichter – Leistungsverluste bei Vorwärtsbetrieb mit
gegebenem Dutycycle [1] | 3
Abbildung 3: Dynamische Parameter des IGBT-Bausteins. [2] | 4
Abbildung 4: Statische Parameter des IGBT-Bausteins – Auszug [2] | 4
Abbildung 5: Profile ähnlicher Kühlkörper und deren Thermischer Widerstand
über der Länge [3] , [4] | 5
Abbildung 6: Anpassung des thermischen Widerstandes mit forcierter Kühlung
[5] | 5
Abbildung 7: Fertigungsorientierte Zeichnung des Kühlkörpers mit
Schnittdarstellung in der unteren linken Ecke | 7
Abbildung 8: Abdeckung der Leiterplatte mit Schraubenlöchern zur Durchsteckmontage und Aussparungen für sämtliche Elemente der Mensch-
Maschine-/ Maschine-Maschine Schnittstelle | 8
Abbildung 9: Explosionsdarstellung des montierten Lüfters und seiner Aufnahme
| 9
Abbildung 10: Abdeckung des Lüfters mit Polygonmuster für die Luftzufuhr. ..... 9 Abbildung 11: Taster, als Einzeldarstellung links und rechts im Gehäuse
eingebaut als Schnittdarstellung | 10
Abbildung 12: Montiertes Gehäuse, links und Explosionszeichnung rechts....... 11

## Verweise

[1] Vishay General Smiconductor, Low V_F Single-Phase In-Line Bridge Rectifiers, Malvern, Pennsylvania: Vishay Interrechnology Inc., 2023.
[2] Infineon Technologies AG, „Control Integrated Power System (CIPOS) IKCM20L60GA Datasheet,“ Infineon Technologies AG, München, 2017.
[3] Fischer Elektronik GmbH & Co.KG, „www.fischerelektronik.de,“ 18 01 2024. [Online]. Available:
https://www.fischerelektronik.de/web_fischer/de_DE/$catalogue/fischerData/PR/SK507_/datasheet.xhtml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. [Zugriff am 18 Januar 01].
[4] Fischer Elektronik GmbH & Co.KG, „www.fischerelektronik.de,“ 18 01 2024. [Online]. Available:
https://www.fischerelektronik.de/web_fischer/de_DE/$catalogue/fischerData/PR/SK507_/datasheet.xhtml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. [Zugriff am 18 01 2024].
[5] Fischer Elektronik GmbH & Co. KG, „www.fischerelektronik.de,“ 2022. [Online]. Available:
https://www.fischerelektronik.de/fileadmin/fischertemplates/download/Katalog/technischeerlaeuterungen_d.pdf. [Zugriff am 05 11 2023].

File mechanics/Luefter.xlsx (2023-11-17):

Strömungsgeschwindigkeit
P_s [W] | I_s [mA] | V_s [V] | dV [m³/h] | L[mm ] | B[mm] | A[m²] | V_s [m/s] | -20% | V_d[m/s] | link
1.14 | 95 | 12 | 13.93 | 40 | 40 | 0.0016 | 2.418402778 | 0.4836805556 | 1.934722222 | https://www.conrad.de/de/p/sunon-ee40101s1-1000u-999-axialluefter-12-v-dc-13-93-m-h-l-x-b-x-h-40-x-40-x-10-mm-1969356.html
1.11 | 92 | 12 | 67.15 | 92 | 92 | 0.008464 | 2.203778093 | 0.4407556186 | 1.763022474 | https://www.conrad.de/de/p/sunon-ef92251s3-1000u-a99-axialluefter-12-v-dc-67-15-m-h-l-x-b-x-h-92-x-92-x-25-mm-2147514.html
3.84 | 200 | 12 | 87 | 92 | 92 | 0.008464 | 2.855229994 | 0.5710459987 | 2.284183995 | https://www.conrad.de/de/p/bequiet-pure-wings-2-92mm-pc-gehaeuse-luefter-schwarz-b-x-h-x-t-92-x-92-x-25-mm-1398967.html
 | 16 | 12 | 76 | 80 | 80 | 0.0064 | 3.298611111 | 0.6597222222 | 2.638888889 | https://www.conrad.de/de/p/logilink-fan102-pc-gehaeuse-luefter-grau-b-x-h-x-t-80-x-80-x-25-mm-871002.html
 |  |  | 18 | 50 | 50 | 0.0025 | 2 | 0.4 | 1.6 | Fabian @ home
 |  |  |  |  |  | 0 | #DIV/0! | #DIV/0! | #DIV/0!
 |  |  |  |  |  | 0 | #DIV/0! | #DIV/0! | #DIV/0!
 |  |  |  |  |  | 0 | #DIV/0! | #DIV/0! | #DIV/0!
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

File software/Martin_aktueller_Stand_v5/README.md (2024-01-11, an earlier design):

new version of 29.11.2023

OneWire Bus programm for the temperature sensor

# Martin_aktueller_Stand_v3 of 27.12.2023
* Ergänzung einer Dokumentation aller wichtigen Klassen
* Befüllen der States Pre_Charge,Standby,RUN mit Logik
* einrichten eines conf.hpp files für alle wichtigen Parameter
* Erstellen eienr FOC_A.hpp für die Erzeugung eines PWM, einschließlich Namespace
* Umschreiben der Templates in der TState_Machine.hpp
* Ergänzung des Interfaces mit den zeigern motor und driver
* kleinere Bug Fixes

# Martin_aktueller_Stand_v4 of 11.01.2024

* bugfixes
* einfügen von Testanweisungen

# Martin_aktueller_Stand_v5 of 11.01.2024

* fehler in Code bei foc behoben
* bei startup inTLA25528 eine error Anweisung entfernt

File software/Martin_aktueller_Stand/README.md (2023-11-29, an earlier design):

new version of 29.11.2023

OneWire Bus programm for the temperature sensor

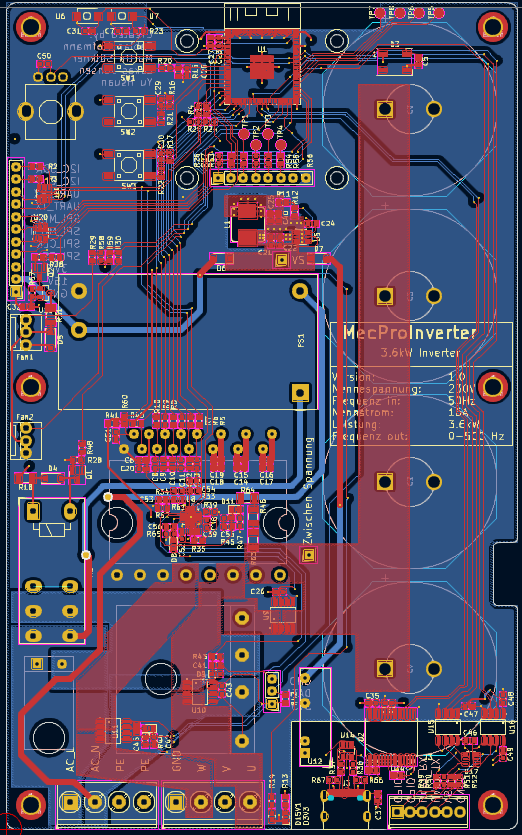
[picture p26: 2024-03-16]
documentation/pictures/Screenshot 2024-01-23 155852.png

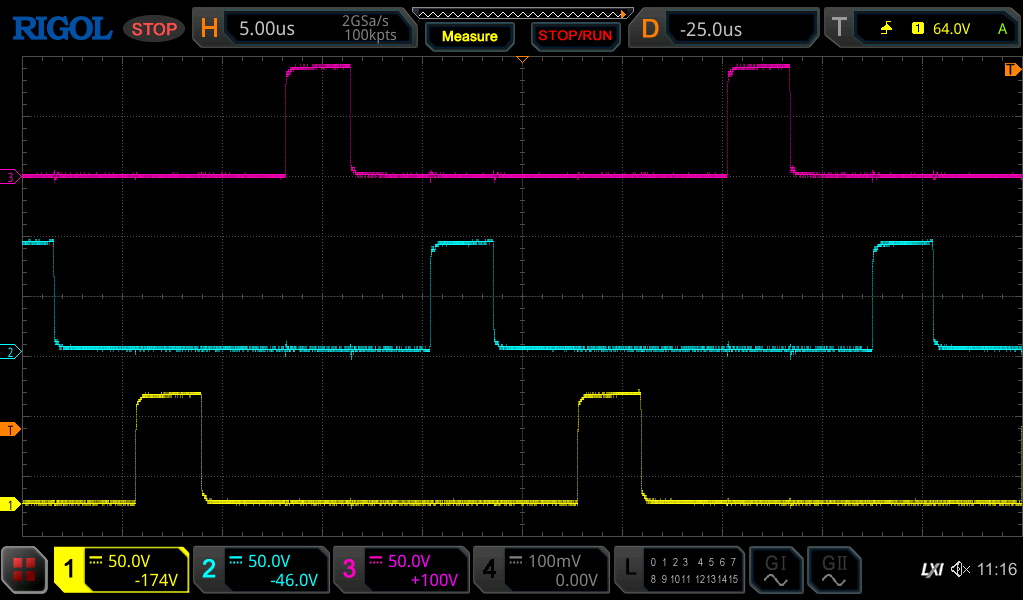
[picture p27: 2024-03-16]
documentation/pictures/Screenshot 2024-01-18 111047.png

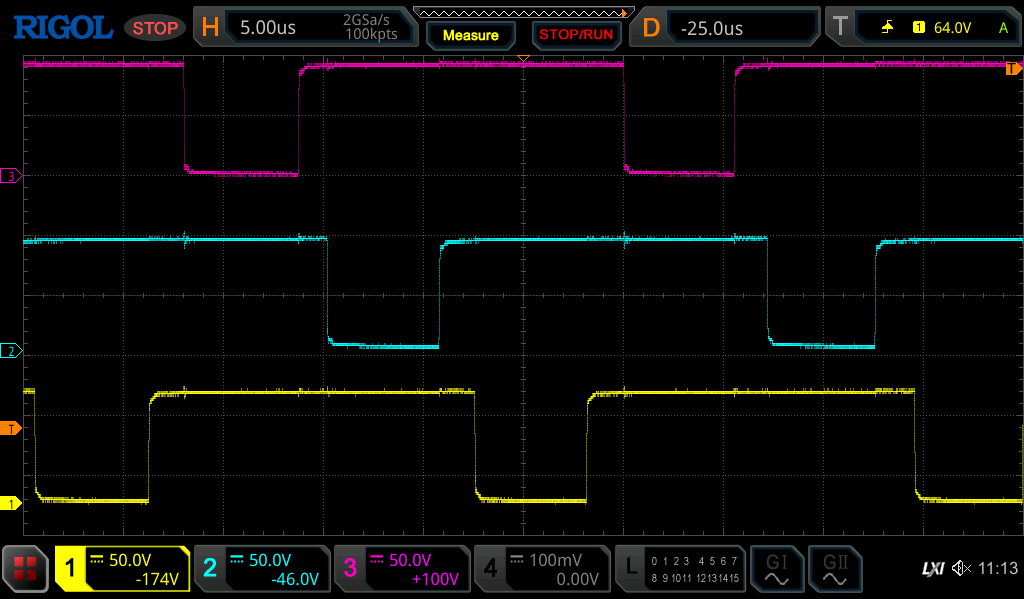
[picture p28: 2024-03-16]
documentation/pictures/Screenshot 2024-01-18 110818.png

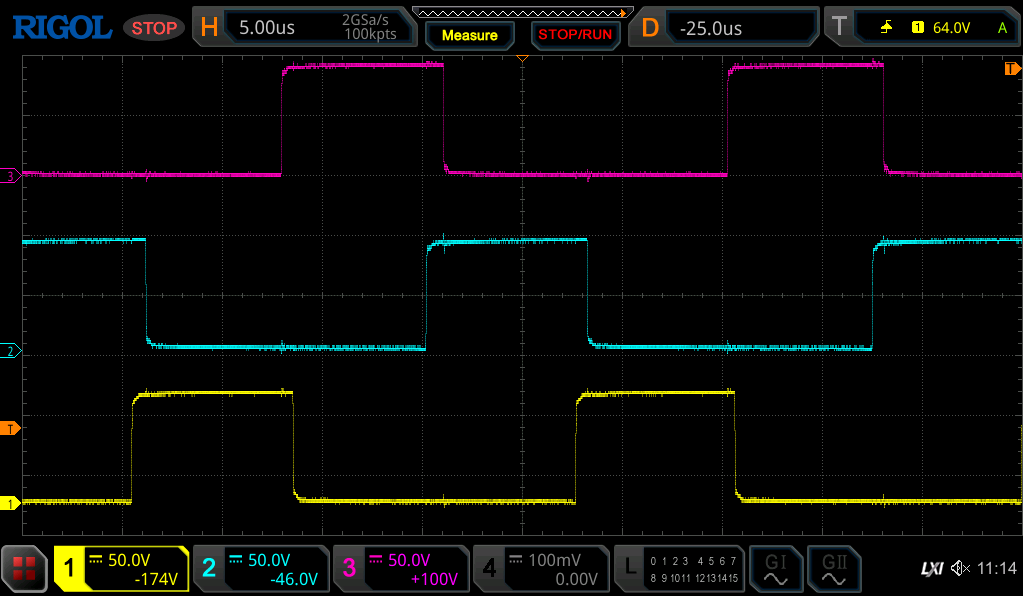
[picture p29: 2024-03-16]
documentation/pictures/Screenshot 2024-01-18 110939.png

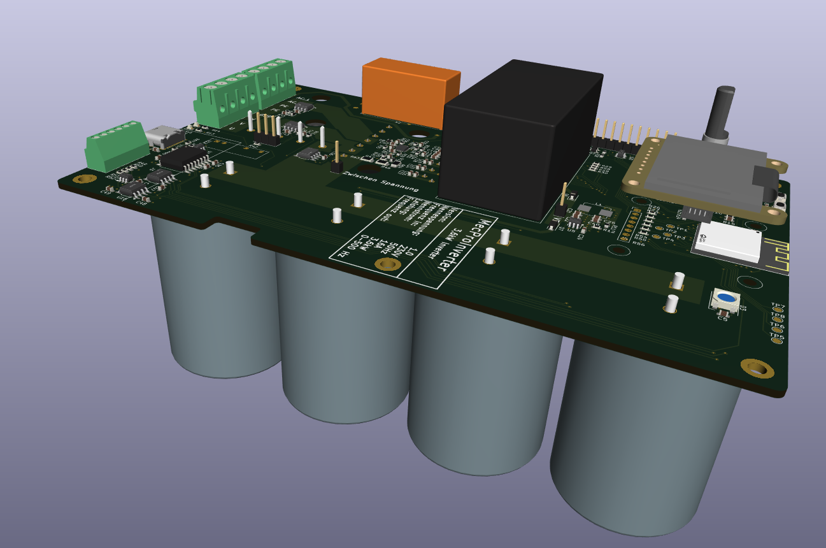
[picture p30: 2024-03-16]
documentation/pictures/Screenshot 2024-01-23 160852.png

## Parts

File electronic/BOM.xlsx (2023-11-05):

 | Komponente | JLC Partnumber | JLC Link
Mikrocontroller | ESP32 S2 Mini
Halbbrücke
Relais
Brückengleichrichter
Spannungswanderl 15V
Spannungswanderl 3,3V
RGB LED
Anschlussterminal Signal
Anschlussterminal Power
USB-C Port
USB Isolator
Stecker Display
Stecker Lüfter
Taster | PTS645SM95SMTR92LFS | C221884 | https://jlcpcb.com/partdetail/ck-PTS645SM95SMTR92LFS/C221884
Potentiometer
Spannungssensor
Stromsensor
RS485 Terminal

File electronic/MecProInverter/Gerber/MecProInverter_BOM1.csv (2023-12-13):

Comment | Designator | Footprint
100nF | C49,C23,C35,C5,C54,C45,C56,C41,C43,C24,C55,C42,C47,C15,C46,C48,C51,C6,C19,C26,C33,C53,C34,C21,C36,C16 | C_0603_1608Metric
LED_3.3V | D3V3 | LED_0603_1608Metric
TestPoint | TP1,TP2,TP3,TP4 | TestPoint_Pad_D1.5mm
10k | R19,R57,R23,R62,R40,R58,R59,R12,R34 | R_0603_1608Metric
D | D8,D9,D10,D11 | D_0603_1608Metric
22uF | C25,C27,C40 | C_0603_1608Metric
10uF | C22,C37,C20 | C_0603_1608Metric
4.7uF | C18,C14,C17 | C_0603_1608Metric
121 | R29,R26,R4,R2,R27,R30,R32,R3 | R_0603_1608Metric
22232031 | Fan1,Fan2 | CONN-TH_3P-P2.54_22-23-2031
TEA1-0505HI | U12 | Converter_DCDC_TRACO_TEA1HI-xxxx_THT
PSRV05-4MR6T1G | U20,U14,U19,U17 | SOT-23-6_L2.9-W1.6-P0.95-LS2.8-BL
10nF | C11,C8,C9,C13,C10,C12 | C_0603_1608Metric
PTS645SM95SMTR92LFS | SW2,SW1,SW3 | KEY-SMD_4P-L6.1-W6.1-P4.50-LS9.0
33k | R64,R63,R46 | R_1206_3216Metric
0 | R54,R55,R53,R56 | R_0603_1608Metric
Test | J7 | PinHeader_1x11_P2.54mm_Vertical
DMN3404L | Q1,Q2 | SOT-23
1uF | C30,C31,C32,C7,C29,C28,C50,C52 | C_0603_1608Metric
~ | H1,H6,H5,H4,H2,H3 | MountingHole_3.2mm_M3_DIN965_Pad_TopBottom
WS2812B | D3 | LED_WS2812B_PLCC4_5.0x5.0mm_P3.2mm
180 | R49,R50,R51,R52 | R_0603_1608Metric
0 | R31 | R_1206_3216Metric
RT314A12 | K2 | Relay_SPDT_Schrack-RT1-16A-FormC_RM5mm
820 | R14,R47 | R_0603_1608Metric
PMV100EPAR | U18 | SOT-23-3_L2.9-W1.3-P1.90-LS2.3-BR
D | D6,D4,D5,D7 | D_SOD-123
5.1k | R66,R67 | R_0603_1608Metric
165 | R8,R10,R48,R6,R9,R38,R5,R7 | R_0603_1608Metric
Motor | J4 | TerminalBlock_Phoenix_PT-1,5-4-5.0-H_1x04_P5.00mm_Horizontal
33.2k | R11 | R_0603_1608Metric
220nF | C38,C39 | C_0603_1608Metric
999M | R35 | R_0603_1608Metric
4,7k | R41 | R_0603_1608Metric
SKRKAEE020 | Reset,Boot | SW-SMD_L3.9-W3.0-P4.45
TPS563201DDCR | U5 | SOT-23-6_L2.9-W1.6-P0.95-LS2.8-BL
100K | R17,R15,R16 | R_0603_1608Metric
ISO_Data | J3 | TerminalBlock_Phoenix_MPT-0,5-6-2.54_1x06_P2.54mm_Horizontal
TYPE-C_16PIN_2MD(073) | U3 | USB-C-SMD_TYPE-C-6PIN-2MD-073
ADUM3160 | U2 | SOIC-16W_7.5x10.3mm_P1.27mm
24 | R37,R36 | R_0603_1608Metric
ADUM1201ARZ-RL7 | U15,U16 | SOIC-8_L4.9-W3.9-P1.27-LS6.0-BL
90 | R18 | R_1206_3216Metric
10M | R44,R43,R65,R45 | R_0603_1608Metric
U_ZK | J8 | PinHeader_1x01_P2.54mm_Vertical
1.8k | R33 | R_0603_1608Metric
MTCK | TP5 | TestPoint_Pad_D1.5mm
1.6k | R24,R25 | R_0603_1608Metric
MTDI | TP8 | TestPoint_Pad_D1.5mm
CC6904SO-30A | U10,U11,U9 | SOP-8_L4.9-W3.9-P1.27-LS6.0-BL
4.7k | R42 | R_0603_1608Metric
Display | J5 | Adafruit_938
U_VS | J9 | PinHeader_1x01_P2.54mm_Vertical
TLA2528IRTER | U8 | WQFN-16_L3.0-W3.0-P0.50-TL-EP1.7
40 | R13 | R_0603_1608Metric
100k | R28 | R_0603_1608Metric
33k | R39 | R_0603_1608Metric
330 | R60 | R_0603_1608Metric
1K | R20,R21 | R_0603_1608Metric
RK09D113000F_10k | U21 | RES-ADJ-TH_RK09D1130C4G
2.2uH | L1 | L_Bourns_SRP7028A_7.3x6.6mm
Net | J10 | TerminalBlock_Phoenix_PT-1,5-4-5.0-H_1x04_P5.00mm_Horizontal
LED_15V | D15V1 | LED_0603_1608Metric
1k | R22 | R_0603_1608Metric
MTDO | TP6 | TestPoint_Pad_D1.5mm
MTMS | TP7 | TestPoint_Pad_D1.5mm
3.3k | R61 | R_0603_1608Metric
ESP32-S3-MINI-1-N8 | U1 | BULETM-SMD_ESP32-S3-MINI-1-N8
MAX312820 | J6 | PinHeader_1x03_P2.54mm_Vertical
IRM-20-15 | PS1 | Converter_ACDC_MeanWell_IRM-20-xx_THT
14. Apr | R1 | PWR220T-20
1mF | C2,C1,C4,C3 | ESMQ351VSN102MA50S
IKCM20L60GA | U13 | DIP-24_L36.0-W21.0-P1.60-LS28.6-TL
LVE2560E | U4 | LVE2560E

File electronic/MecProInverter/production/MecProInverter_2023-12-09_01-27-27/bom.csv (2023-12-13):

Designator | Footprint | Quantity | Value | LCSC Part #
C1, C2, C3, C4 | ESMQ351VSN102MA50S | 4 | 1mF
C10, C11, C12, C13, C8, C9 | 0603 | 6 | 10nF
C14, C17, C18 | 0603 | 3 | 4.7uF
C15, C16, C19, C21, C23, C24, C26, C33, C34, C35, C36, C38, C39, C41, C42, C43, C45, C46, C47, C48, C49, C5, C51, C53, C54, C55, C56, C6 | 0603 | 28 | 100nF
C20, C22, C25, C27, C37, C40 | 0603 | 6 | 22uF
C28, C29, C30, C31, C32, C50, C52, C7 | 0603 | 8 | 1uF
D10, D11, D8, D9 | 0603 | 4 | D
D15V1 | 0603 | 1 | LED_15V
D3 | LED_WS2812B_PLCC4_5.0x5.0mm_P3.2mm | 1 | WS2812B
D3V3 | 0603 | 1 | LED_3.3V
D4, D5, D6, D7 | D_SOD-123 | 4 | D
Fan1, Fan2 | CONN-TH_3P-P2.54_22-23-2031 | 2 | 0022232031 | 0022232031
H1, H2, H3, H4, H5, H6 | MountingHole_3.2mm_M3_DIN965_Pad_TopBottom | 6 | ~
J10 | TerminalBlock_Phoenix_PT-1,5-4-5.0-H_1x04_P5.00mm_Horizontal | 1 | Net
J3 | TerminalBlock_Phoenix_MPT-0,5-6-2.54_1x06_P2.54mm_Horizontal | 1 | ISO_Data
J4 | TerminalBlock_Phoenix_PT-1,5-4-5.0-H_1x04_P5.00mm_Horizontal | 1 | Motor
J5 | Adafruit_938 | 1 | Display
J6 | PinHeader_1x03_P2.54mm_Vertical | 1 | MAX312820
J7 | PinHeader_1x11_P2.54mm_Vertical | 1 | Test
J8 | PinHeader_1x01_P2.54mm_Vertical | 1 | U_ZK
J9 | PinHeader_1x01_P2.54mm_Vertical | 1 | U_VS
K2 | Relay_SPDT_Schrack-RT1-16A-FormC_RM5mm | 1 | RT314A12
L1 | L_Bourns_SRP7028A_7.3x6.6mm | 1 | 2.2uH
PS1 | Converter_ACDC_MeanWell_IRM-20-xx_THT | 1 | IRM-20-15
Q1, Q2 | SOT-23 | 2 | DMN3404L
R1 | PWR220T-20 | 1 | 14.4
R10, R13, R2, R26, R27, R29, R3, R30, R32, R38, R4, R48, R49, R5, R50, R51, R52, R6, R7, R8, R9 | 0603 | 21 | 121
R11, R39 | 0603 | 2 | 33k
R12, R19, R23, R28, R34, R40, R57, R58, R59, R62 | 0603 | 10 | 10k
R14, R47 | 0603 | 2 | 820
R15, R16, R17 | 0603 | 3 | 100K
R18 | 1206 | 1 | 90
R20, R21, R22 | 0603 | 3 | 1K
R24, R25 | 0603 | 2 | 1.6k
R31 | 1206 | 1 | 0
R33 | 0603 | 1 | 1.8k
R35 | 0603 | 1 | 999M
R36, R37 | 0603 | 2 | 24
R41 | 0603 | 1 | 3,3k
R42 | 0603 | 1 | 4.7k
R43, R44, R45, R65 | 0603 | 4 | 10M
R46, R63, R64 | 1206 | 3 | 33k
R53, R54, R55, R56 | 0603 | 4 | 0
R60 | 0603 | 1 | 330
R61 | 0603 | 1 | 3.3k
R66, R67 | 0603 | 2 | 5.1k
SW1, SW2, SW3 | KEY-SMD_4P-L6.1-W6.1-P4.50-LS9.0 | 3 | PTS645SM95SMTR92LFS | C221884
TP1, TP2, TP3, TP4 | TestPoint_Pad_D1.5mm | 4 | TestPoint
TP5 | TestPoint_Pad_D1.5mm | 1 | MTCK
TP6 | TestPoint_Pad_D1.5mm | 1 | MTDO
TP7 | TestPoint_Pad_D1.5mm | 1 | MTMS
TP8 | TestPoint_Pad_D1.5mm | 1 | MTDI
U1 | BULETM-SMD_ESP32-S3-MINI-1-N8 | 1 | ESP32-S3-MINI-1-N8
U10, U11, U9 | SOP-8_L4.9-W3.9-P1.27-LS6.0-BL | 3 | CC6904SO-30A | C521203
U12 | Converter_DCDC_TRACO_TEA1HI-xxxx_THT | 1 | TEA1-0505HI
U13 | DIP-24_L36.0-W21.0-P1.60-LS28.6-TL | 1 | IKCM20L60GA | C536161
U14, U17, U19, U20 | SOT-23-6_L2.9-W1.6-P0.95-LS2.8-BL | 4 | PSRV05-4MR6T1G | C2936987
U15, U16 | SOIC-8_L4.9-W3.9-P1.27-LS6.0-BL | 2 | ADUM1201ARZ-RL7 | C9669
U18 | SOT-23-3_L2.9-W1.3-P1.90-LS2.3-BR | 1 | PMV100EPAR | C3290636
U2 | SOIC-16W_7.5x10.3mm_P1.27mm | 1 | ADUM3160
U21 | RES-ADJ-TH_RK09D1130C4G | 1 | RK09D113000F_10k | C470317
U3 | USB-C-SMD_TYPE-C-6PIN-2MD-073 | 1 | TYPE-C_16PIN_2MD(073) | C2765186
U4 | LVE2560E | 1 | LVE2560E
U5 | SOT-23-6_L2.9-W1.6-P0.95-LS2.8-BL | 1 | TPS563201DDCR | C116592
U6, U7 | SW-SMD_L3.9-W3.0-P4.45 | 2 | SKRKAEE020 | C115357
U8 | WQFN-16_L3.0-W3.0-P0.50-TL-EP1.7 | 1 | TLA2528IRTER | C2866175

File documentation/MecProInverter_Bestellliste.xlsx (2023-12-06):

Pos. | Modul | Name | Distributor | Bemerkung | Link | Anzahl | Kosten pro Stück/€ | Kosten/€ | Status
1 | Elektronik
2 |  |  |  |  |  |  |  | 0
3 | Kondensator | ESMQ351VSN102MA50S | Mouser |  | https://www.mouser.de/ProductDetail/Chemi-Con/ESMQ351VSN102MA50S?qs=xI6Y96ivSIymLA4AkGqstA%3D%3D | 4 | 5.4 | 21.6
4 | Halbbrücke | IKCM20H60GA | Mouser |  | https://www.mouser.de/ProductDetail/Infineon-Technologies/IKCM20L60GA?qs=geqVyQakq09sMqSgPnylYg%3D%3D | 0 | 13.8 | 0
5 | Relais | RTD14012F | Mouser |  | https://eu.mouser.com/ProductDetail/TE-Connectivity-PB/RTD14012F?qs=wG8I%2FCOA%2FTuTYxE%252BmbBPYA%3D%3D | 1 | 5 | 5
6 | Brückengleichrichter | LVE2560E-M3/P | Mouser |  | https://www.mouser.de/ProductDetail/Vishay-Semiconductors/LVE2560E-M3-P | 1 | 4.57 | 4.57
7 | Power Terminal | 651-1935187 | Mouser |  | https://www.mouser.de/ProductDetail/Phoenix-Contact/1935187?qs=W3wJikR1%252BS5tIYApIw6HoQ%3D%3D | 4 | 0.93 | 3.72
8 | Spannungswandler 15Volt | IRM-20-15 | Mouser |  | https://eu.mouser.com/ProductDetail/MEAN-WELL/IRM-20-15?qs=WkdRfq4wf1Ne04vP4qNfjQ%3D%3D | 1 | 11.4 | 11.4
9 | Lüfter Stecker | Molex22-23-2031 | Mouser |  | https://eu.mouser.com/ProductDetail/Molex/22-23-2031?qs=ILqg114nvd41XyIAFDpXfw%3D%3D | 10 | 0.17 | 1.7
10 | Temperatursensor | LM61CIZ | Mouser |  | https://www.mouser.de/ProductDetail/Analog-Devices-Maxim-Integrated/MAX31820MCR%2b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 | 1 | 1.37 | 1.37
11 | Display | Adafruit 938 | Mouser |  | https://www.mouser.de/ProductDetail/Adafruit/938?qs=GURawfaeGuBw18l06EFBdw%3D%3D | 1 | 18.555 | 18.555
12 | Spannungswandler 5V-5V | TEA 1-0505HI | Mouser |  | https://www.mouser.de/ProductDetail/TRACO-Power/TEA-1-0505HI?qs=GedFDFLaBXGYgii%2FlopLEg%3D%3D&gad_source=1 | 1 | 2.1 | 2.1
13 | Signal Terminal | TB001-500-06BE | Mouser |  | https://www.mouser.de/ProductDetail/CUI-Devices/TB001-500-06BE | 10 | 0.54 | 5.4
14 | Potentiometer | RK09D113000K | Mouser |  | https://www.mouser.de/ProductDetail/Alps-Alpine/RK09D113000K?qs=oKW7zmyQiO5%2FMNsP8zcsfA%3D%3D | 2 | 0.89 | 1.78
15 | Keramik Kondensator | C1210C104MBRACTU | Mouser |  | https://www.mouser.de/ProductDetail/KEMET/C1210C104MBRACTU?qs=%2FukktrhNKsZSienwvzOPlQ%3D%3D | 10 | 0.21 | 2.1
16 | Leistungswiderstand | PWR220T-20-15R0F | Mouser |  | https://www.mouser.de/ProductDetail/Bourns/PWR220T-20-15R0F?qs=%2FxQVPCMPNziUrCAUz897Iw%3D%3D | 2 | 3.42 | 6.84
17 |  |  |  |  |  |  |  | 0
18 |  |  |  |  |  |  |  | 0
19 |  |  |  |  |  |  |  | 0
20 |  |  |  |  |  |  |  | 0
21 |  |  |  |  |  |  |  | 0
22 | Mechanik |  |  |  |  |  |  | 0
23 |  |  |  |  |  |  |  | 0
24 |  |  |  |  |  |  |  | 0
25 |  |  |  |  |  |  |  | 0
26 |  |  |  |  |  |  |  | 0
27 |  |  |  |  |  |  |  | 0
28 |  |  |  |  |  |  |  | 0
29 |  |  |  |  |  |  |  | 0
30 |  |  |  |  |  |  |  | 0
31 |  |  |  |  |  |  |  | 0
32 |  |  |  |  |  |  |  | 0
33 |  |  |  |  |  |  |  | 0
34 |  |  |  |  |  |  |  | 0
35 |  |  |  |  |  |  |  | 86.135

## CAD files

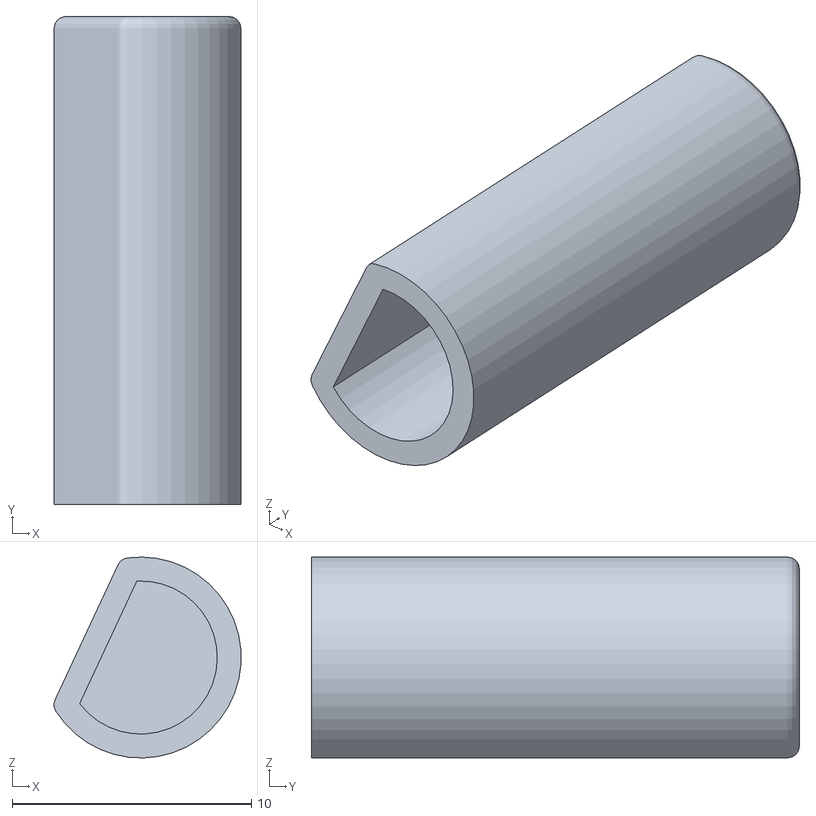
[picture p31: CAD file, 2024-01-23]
mechanics/Gehäuse/Poti_Verlaengerung.stl
7.82 x 20.4 x 8.40

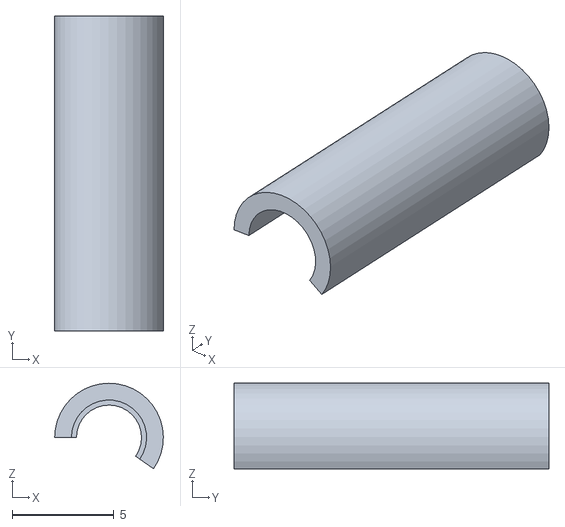
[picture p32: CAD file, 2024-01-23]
mechanics/Gehäuse/Fuehrung_Taster.stl
5.35 x 15.5 x 4.21

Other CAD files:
mechanics/Aufnahme_Fan.ipt
mechanics/Aufnahme_Fan_02.ipt
mechanics/BrueckenGR_LVE2560E.iam
mechanics/BrueckenGR_LVE2560E.ipt
mechanics/BrueckenGR_LVE2560E_Feet.ipt
mechanics/CIPOS.ipt
mechanics/Fan_Assembled.iam
mechanics/Feder.ipt
mechanics/Fenster_LED.ipt
mechanics/Fenster_OLED.ipt
mechanics/Fuehrung_Taster.ipt
mechanics/Housing_TOP_ASM.iam
mechanics/Housing_Top_V2_2.ipt
mechanics/Kuehlkoerper.ipt
mechanics/Poti_Verlaengerung.ipt
mechanics/Spacer.ipt
mechanics/Taster.ipt
mechanics/Taster_Top.ipt

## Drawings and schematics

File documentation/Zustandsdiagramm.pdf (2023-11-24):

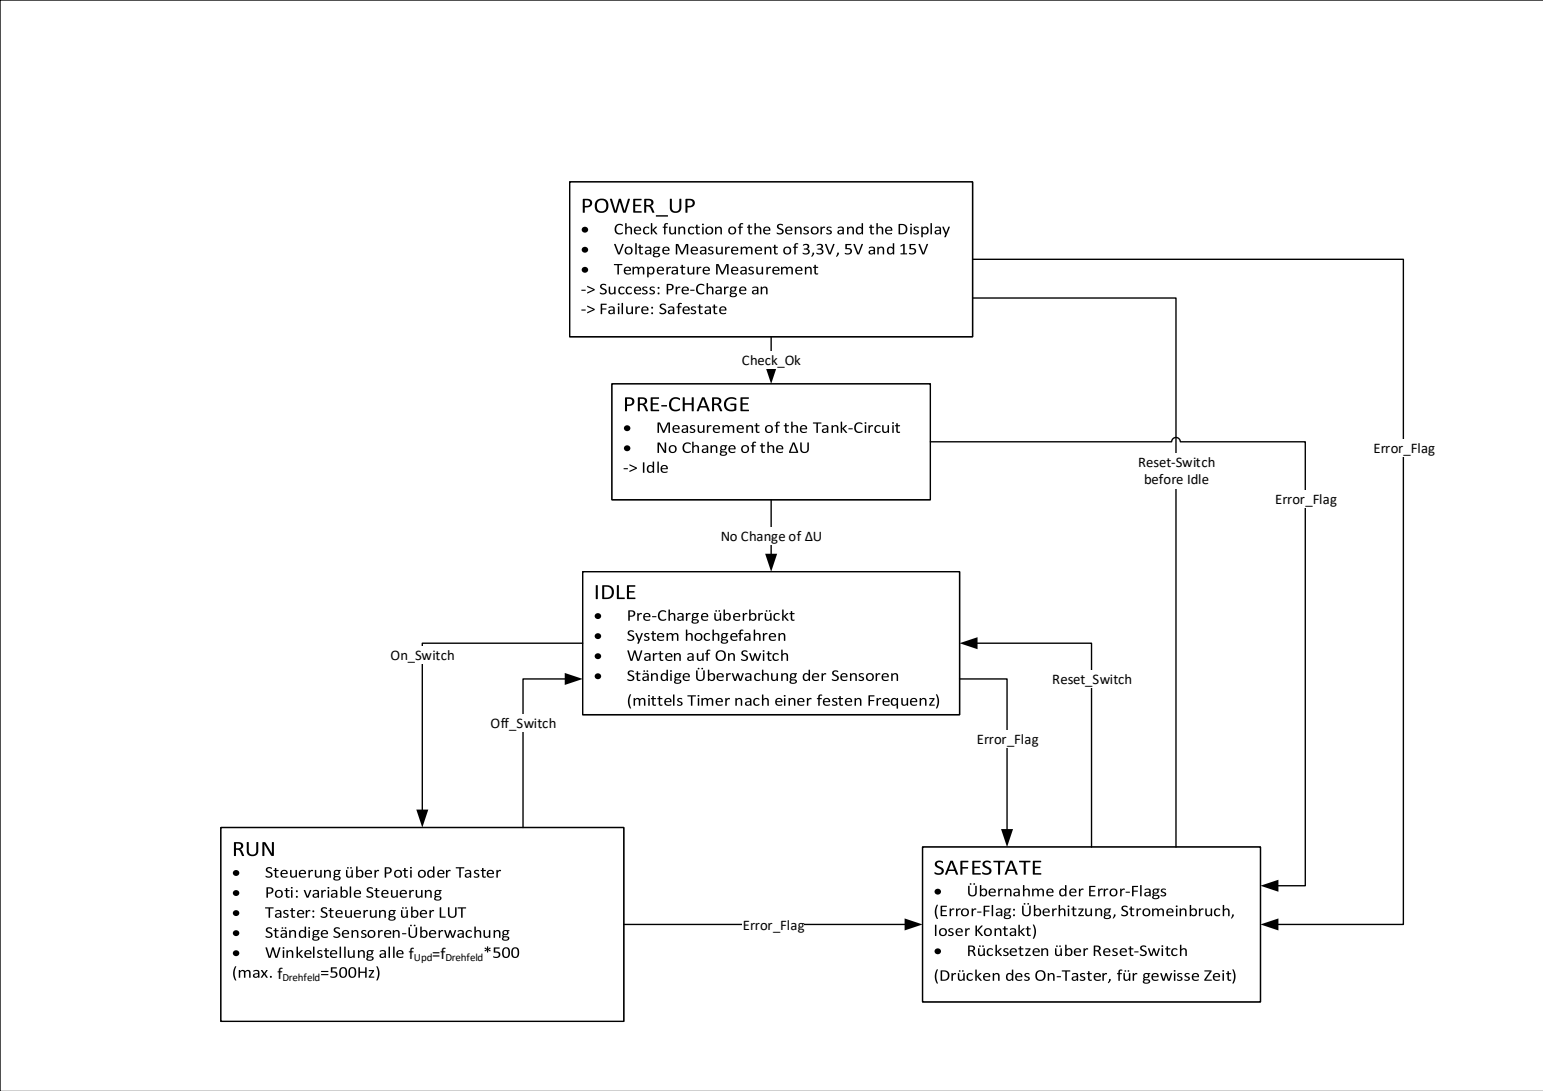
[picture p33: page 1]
fUpd=fDrehfeld; fDrehfeld; On_Switch; Reset_Switch; Error_Flag; Check_Ok

Error_Flag

Reset-Switch before Idle

No Change of ΔU

Off_Switch

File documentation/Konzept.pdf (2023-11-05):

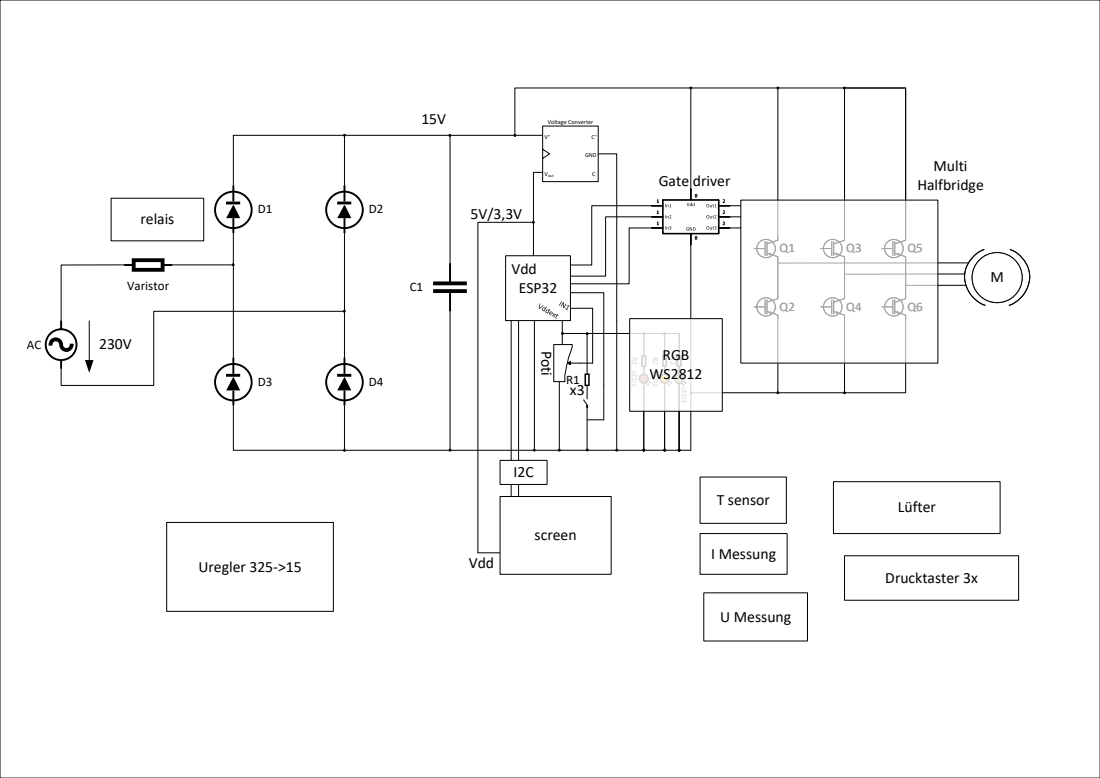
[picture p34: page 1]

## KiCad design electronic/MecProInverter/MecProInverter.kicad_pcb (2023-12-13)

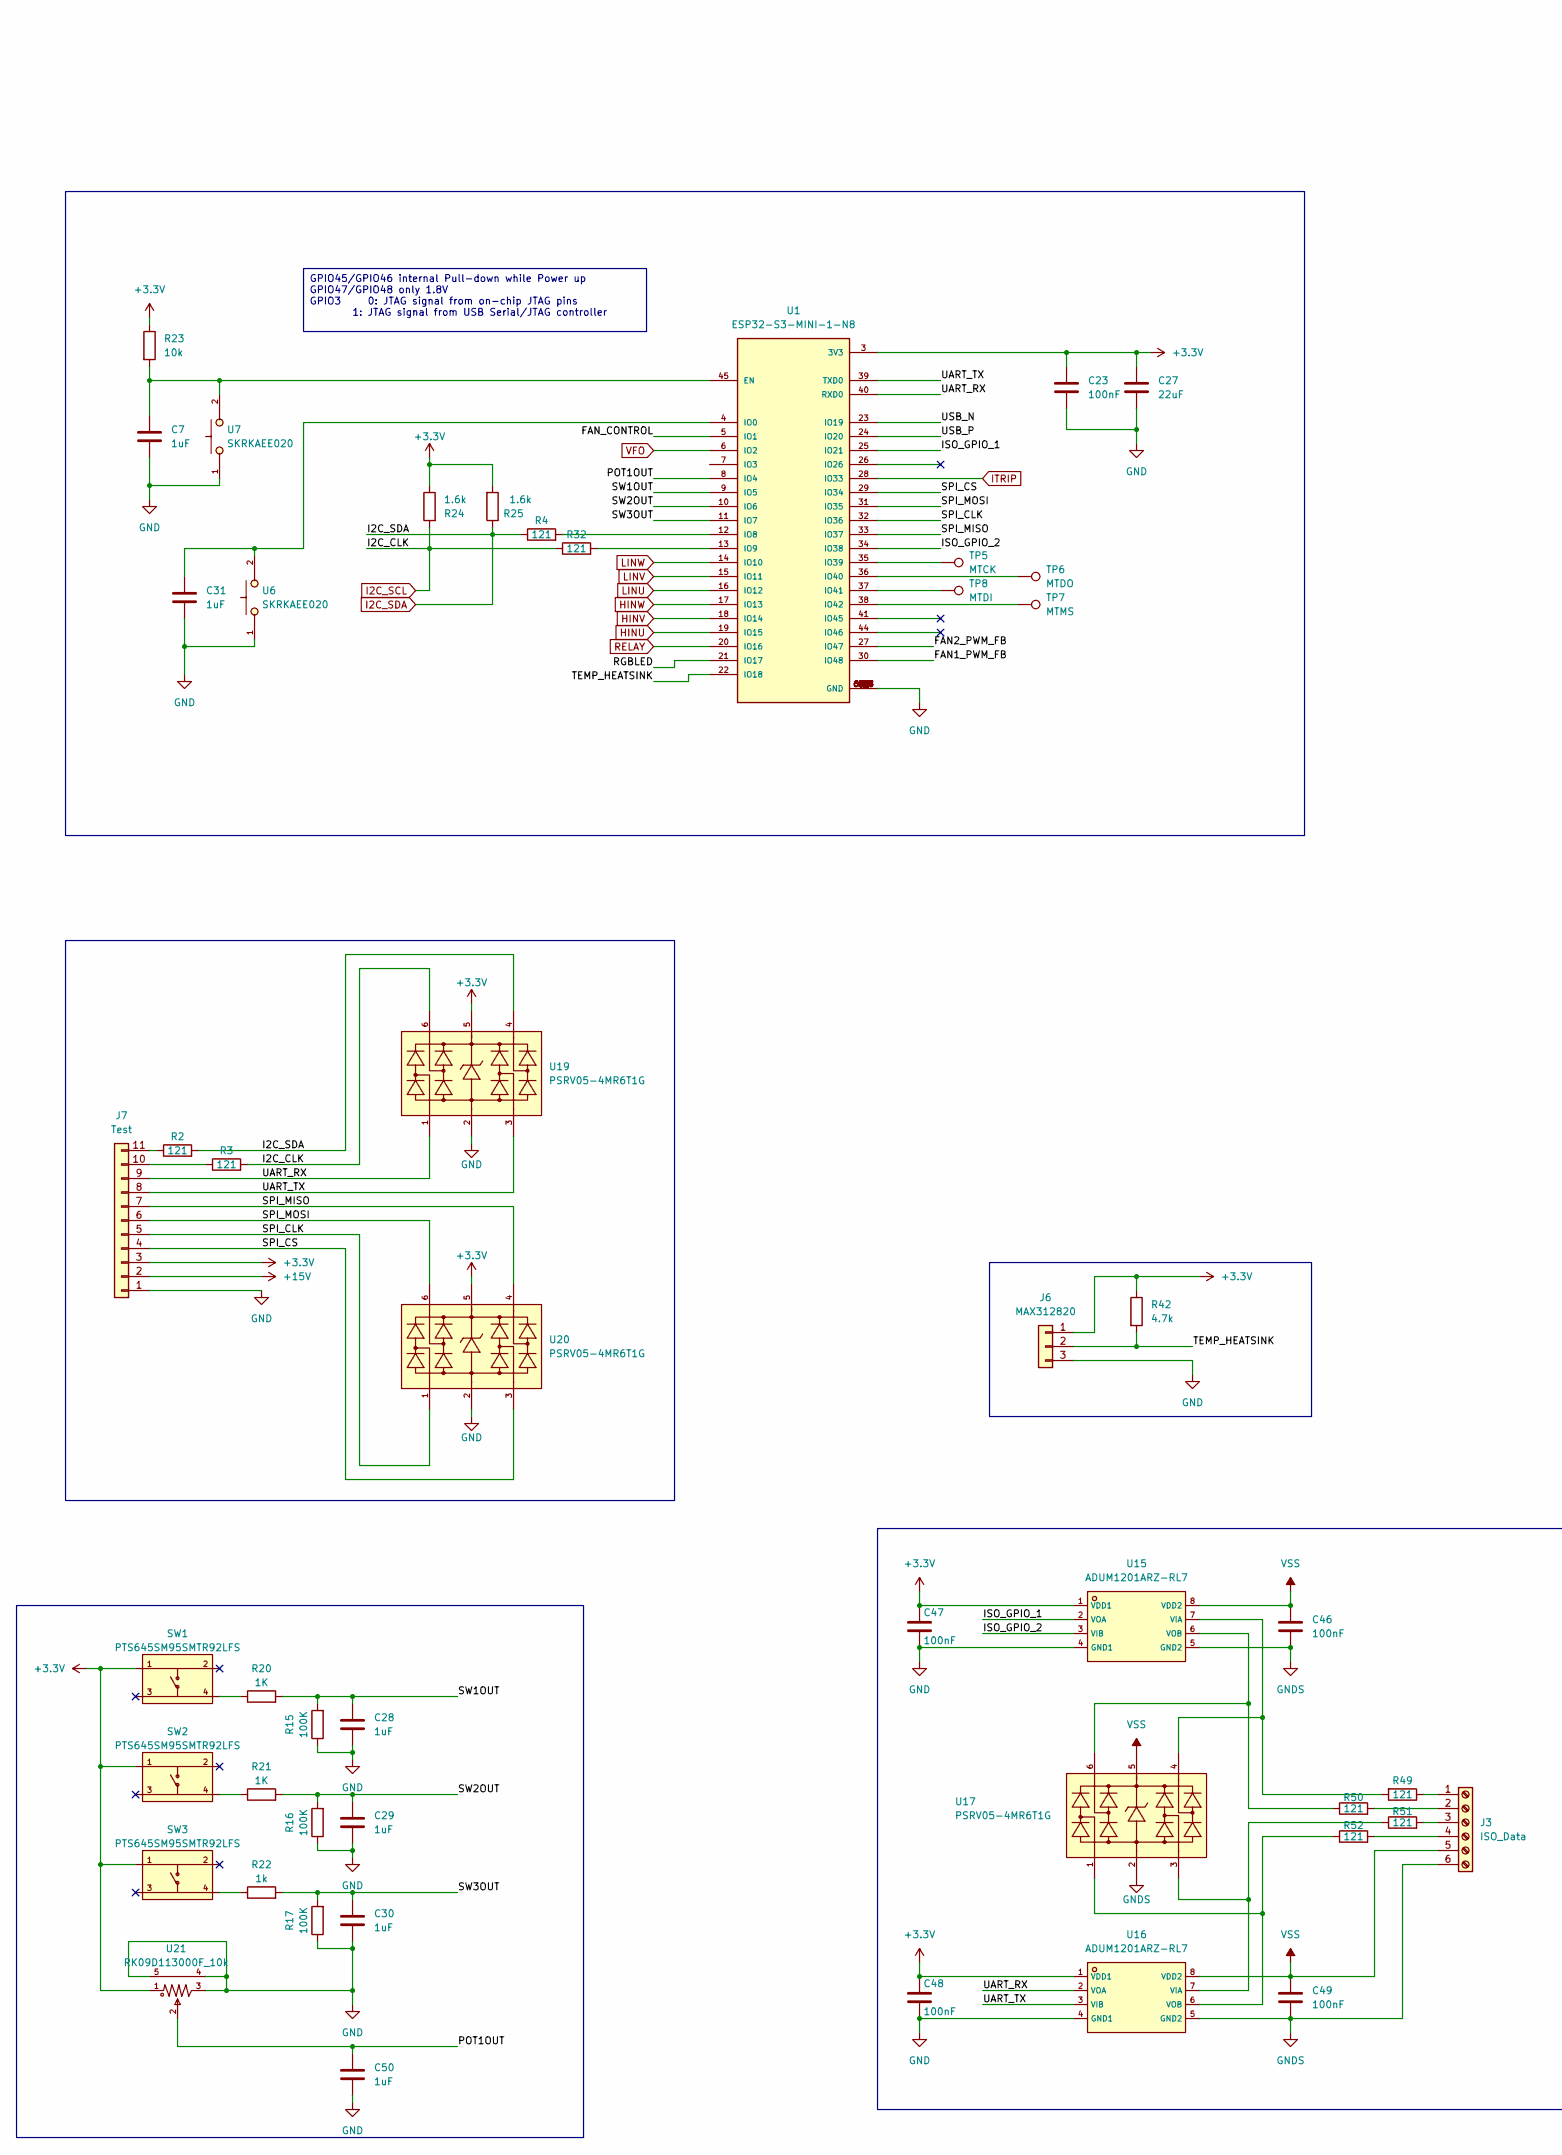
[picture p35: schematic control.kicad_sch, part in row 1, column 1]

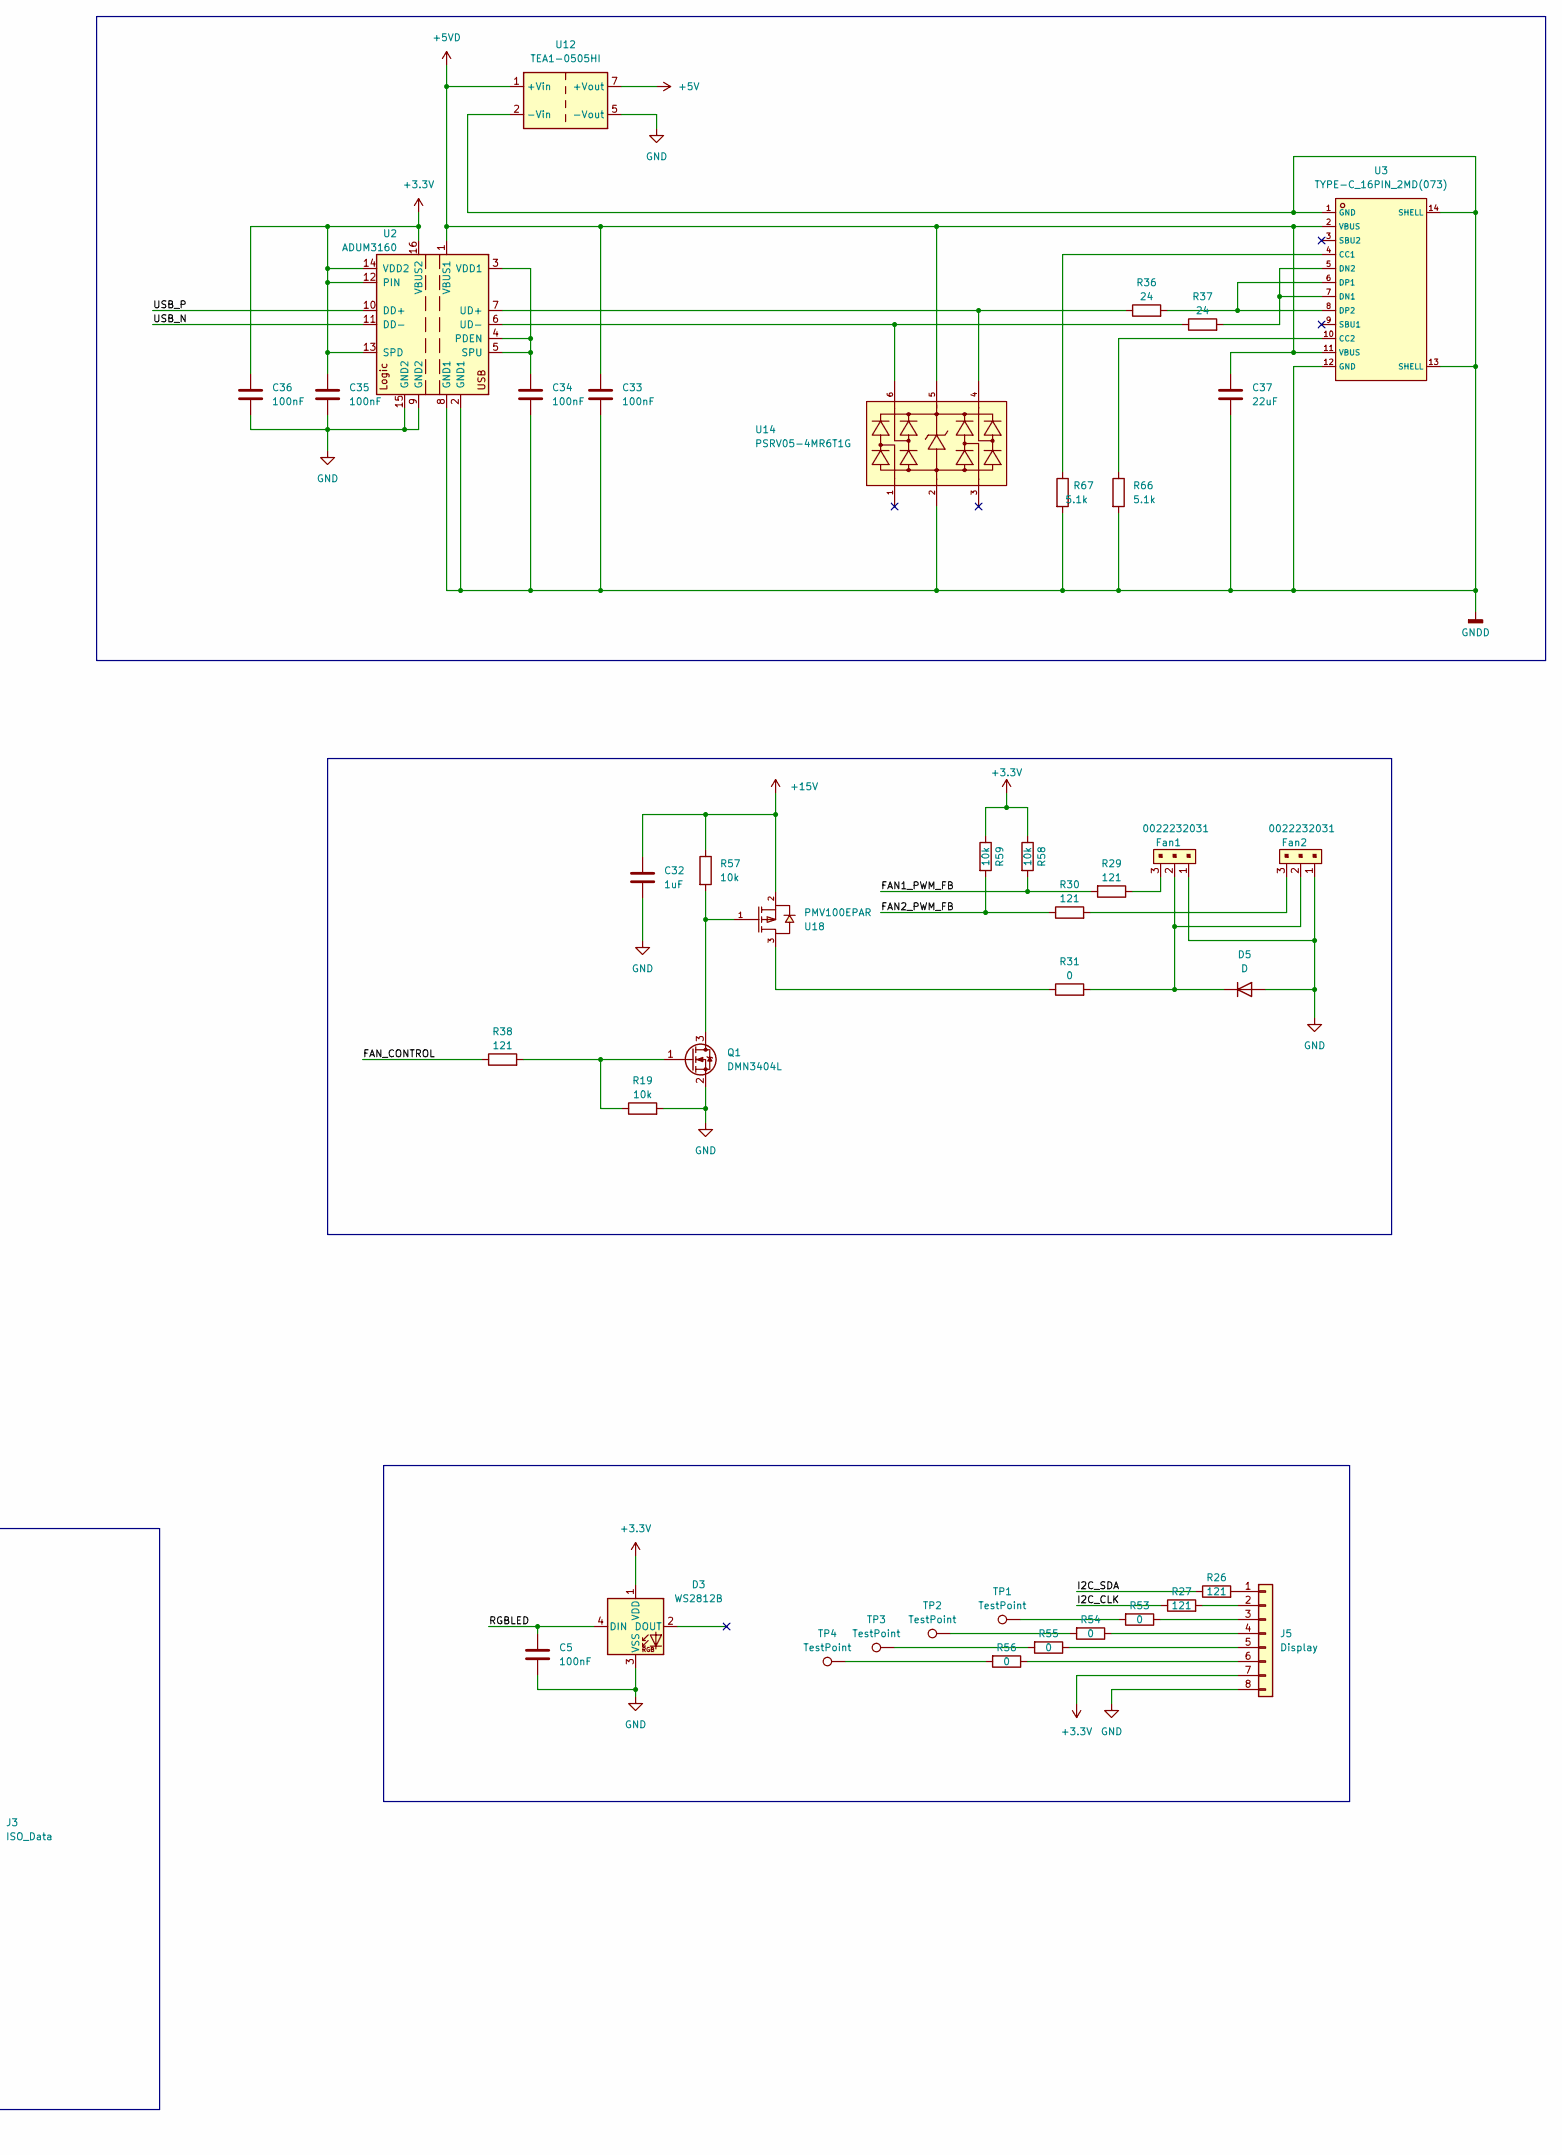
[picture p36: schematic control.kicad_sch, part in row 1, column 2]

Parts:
C5, C23, C33, C34, C35, C36, C46, C47, C48, C49: 100nF; C_0603_1608Metric
C7, C28, C29, C30, C31, C32, C50: 1uF; C_0603_1608Metric
C27, C37: 22uF; C_0603_1608Metric
D3: WS2812B; LED_WS2812B_PLCC4_5.0x5.0mm_P3.2mm
D5: D; D_SOD-123
Fan1, Fan2: 0022232031; CONN-TH_3P-P2.54_22-23-2031; MPN 0022232031; Digi-Key_PN WM4201-ND
J3: ISO_Data; TerminalBlock_Phoenix_MPT-0,5-6-2.54_1x06_P2.54mm_Horizontal
J5: Display; Adafruit_938
J6: MAX312820; PinHeader_1x03_P2.54mm_Vertical
J7: Test; PinHeader_1x11_P2.54mm_Vertical
Q1: DMN3404L; SOT-23
R2, R3, R4, R26, R27, R29, R30, R32, R38, R49, R50, R51, R52: 121; R_0603_1608Metric
R15, R16, R17: 100K; R_0603_1608Metric
R19, R23, R57, R58, R59: 10k; R_0603_1608Metric
R20, R21: 1K; R_0603_1608Metric
R22: 1k; R_0603_1608Metric
R24, R25: 1.6k; R_0603_1608Metric
R31: 0; R_1206_3216Metric
R36, R37: 24; R_0603_1608Metric
R42: 4.7k; R_0603_1608Metric
R53, R54, R55, R56: 0; R_0603_1608Metric
R66, R67: 5.1k; R_0603_1608Metric
SW1, SW2, SW3: PTS645SM95SMTR92LFS; KEY-SMD_4P-L6.1-W6.1-P4.50-LS9.0; LCSC C221884
TP1, TP2, TP3, TP4: TestPoint; TestPoint_Pad_D1.5mm
TP5: MTCK; TestPoint_Pad_D1.5mm
TP6: MTDO; TestPoint_Pad_D1.5mm
TP7: MTMS; TestPoint_Pad_D1.5mm
TP8: MTDI; TestPoint_Pad_D1.5mm
U1: ESP32-S3-MINI-1-N8; BULETM-SMD_ESP32-S3-MINI-1-N8; PARTREV v0.6
U2: ADUM3160; SOIC-16W_7.5x10.3mm_P1.27mm
U3: TYPE-C_16PIN_2MD(073); USB-C-SMD_TYPE-C-6PIN-2MD-073; LCSC C2765186
U6, U7: SKRKAEE020; SW-SMD_L3.9-W3.0-P4.45; LCSC C115357
U12: TEA1-0505HI; Converter_DCDC_TRACO_TEA1HI-xxxx_THT
U14, U17, U19, U20: PSRV05-4MR6T1G; SOT-23-6_L2.9-W1.6-P0.95-LS2.8-BL; LCSC C2936987
U15, U16: ADUM1201ARZ-RL7; SOIC-8_L4.9-W3.9-P1.27-LS6.0-BL; LCSC C9669
U18: PMV100EPAR; SOT-23-3_L2.9-W1.3-P1.90-LS2.3-BR; LCSC C3290636
U21: RK09D113000F_10k; RES-ADJ-TH_RK09D1130C4G; LCSC C470317

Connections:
+3.3V: C23.1, C27.1, C35.1, C36.1, C47.1, C48.1, D3.1 (VDD), J5.7, J6.1, J7.3, R23.1, R24.1, R25.2, R42.1, R58.1, R59.1, SW1.1, SW2.1, SW3.1, U1.3 (3V3), U2.12 (PIN), U2.13 (SPD), U2.14 (VDD2), U2.16 (VBUS2), U15.1 (VDD1), U16.1 (VDD1), U19.5, U20.5, U21.1; also elsewhere on the board
+5V: U12.7 (+Vout); also elsewhere on the board
+5VD: C33.1, C37.1, U2.1 (VBUS1), U3.2 (VBUS), U3.11 (VBUS), U12.1 (+Vin), U14.5
+15V: C32.1, J7.2, R57.1, U18.2 (S); also elsewhere on the board
/Control/FAN1_PWM_FB: R29.2, R58.2, U1.30 (IO48)
/Control/FAN2_PWM_FB: R30.1, R59.2, U1.27 (IO47)
/Control/FAN_CONTROL: R38.1, U1.5 (IO1)
/Control/ISO_GPIO_1: U1.25 (IO21), U15.2 (VOA)
/Control/ISO_GPIO_2: U1.34 (IO38), U15.3 (VIB)
/Control/POT1OUT: C50.1, U1.8 (IO4), U21.2
/Control/RGBLED: C5.1, D3.4 (DIN), U1.21 (IO17)
/Control/SPI_CLK: J7.5, U1.32 (IO36), U20.1
/Control/SPI_CS: J7.4, U1.29 (IO34), U20.3
/Control/SPI_MISO: J7.7, U1.33 (IO37), U20.4
/Control/SPI_MOSI: J7.6, U1.31 (IO35), U20.6
/Control/SW1OUT: C28.1, R15.2, R20.2, U1.9 (IO5)
/Control/SW2OUT: C29.1, R16.2, R21.2, U1.10 (IO6)
/Control/SW3OUT: C30.1, R17.2, R22.2, U1.11 (IO7)
/Control/TEMP_HEATSINK: J6.2, R42.2, U1.22 (IO18)
/Control/UART_RX: J7.9, U1.40 (RXD0), U16.2 (VOA), U19.1
/Control/UART_TX: J7.8, U1.39 (TXD0), U16.3 (VIB), U19.3
/Control/USB_N: U1.23 (IO19), U2.11 (DD-)
/Control/USB_P: U1.24 (IO20), U2.10 (DD+)
GND: C5.2, C7.2, C23.2, C27.2, C28.2, C29.2, C30.2, C31.2, C32.2, C35.2, C36.2, C47.2, C48.2, C50.2, D3.3 (VSS), D5.2 (A), Fan1.1, Fan2.1, J5.8, J6.3, J7.1, Q1.2 (S), R15.1, R16.1, R17.1, R19.2, U1.1 (GND), U1.2 (GND), U1.42 (GND), U1.43 (GND), U1.46 (GND), U1.47 (GND), U1.48 (GND), U1.49 (GND), U1.50 (GND), U1.51 (GND), U1.52 (GND), U1.53 (GND), U1.54 (GND), U1.55 (GND), U1.56 (GND), U1.57 (GND), U1.58 (GND), U1.59 (GND), U1.60 (GND), U1.61 (GND), U1.61_1 (GND), U1.61_2 (GND), U1.61_3 (GND), U1.61_4 (GND), U1.61_5 (GND), U1.61_6 (GND), U1.61_7 (GND), U1.61_8 (GND), U1.62 (GND), U1.63 (GND), U1.64 (GND), U1.65 (GND), U2.9 (GND2), U2.15 (GND2), U6.1, U7.1, U12.5 (-Vout), U15.4 (GND1), U16.4 (GND1), U19.2, U20.2, U21.3, U21.4, U21.5; also elsewhere on the board
GNDD: C33.2, C34.2, C37.2, R66.2, R67.2, U2.2 (GND1), U2.8 (GND1), U3.1 (GND), U3.12 (GND), U3.13 (SHELL), U3.14 (SHELL), U12.2 (-Vin), U14.2
GNDS: C46.2, C49.2, J3.6, U15.5 (GND2), U16.5 (GND2), U17.2
HINU: U1.19 (IO15); also elsewhere on the board
HINV: U1.18 (IO14); also elsewhere on the board
HINW: U1.17 (IO13); also elsewhere on the board
I2C_SCL: R3.2, R24.2, R27.1, R32.1, U19.6; also elsewhere on the board
I2C_SDA: R2.2, R4.1, R25.1, R26.1, U19.4; also elsewhere on the board
ITRIP: U1.28 (IO33); also elsewhere on the board
LINU: U1.16 (IO12); also elsewhere on the board
LINV: U1.15 (IO11); also elsewhere on the board
LINW: U1.14 (IO10); also elsewhere on the board
unnamed: D5.1 (K), Fan1.2, Fan2.2, R31.2
unnamed: Fan1.3, R29.1
unnamed: Fan2.3, R30.2
unnamed: J3.1, R49.1
unnamed: J3.2, R50.2
unnamed: J3.3, R51.2
unnamed: J3.4, R52.2
unnamed: J5.1, R26.2
unnamed: J5.2, R27.2
unnamed: J5.3, R53.1
unnamed: J5.4, R54.1
unnamed: J5.5, R55.1
unnamed: J5.6, R56.1
unnamed: J7.10, R3.1
unnamed: J7.11, R2.1
unnamed: R20.1, SW1.4
unnamed: R21.1, SW2.4
unnamed: R22.1, SW3.4
unnamed: R53.2, TP1.1
unnamed: R54.2, TP2.1
unnamed: R55.2, TP3.1
unnamed: R56.2, TP4.1
unnamed: C7.1, R23.2, U1.45 (EN), U7.2
unnamed: C31.1, U1.4 (IO0), U6.2
unnamed: R4.2, U1.12 (IO8)
unnamed: R32.2, U1.13 (IO9)
unnamed: TP5.1, U1.35 (IO39)
unnamed: TP6.1, U1.36 (IO40)
unnamed: TP8.1, U1.37 (IO41)
unnamed: TP7.1, U1.38 (IO42)
unnamed: C34.1, U2.3 (VDD1), U2.4 (PDEN), U2.5 (SPU)
unnamed: R36.1, U2.7 (UD+), U14.4
unnamed: R37.1, U2.6 (UD-), U14.6
unnamed: R67.1, U3.4 (CC1)
unnamed: R66.1, U3.10 (CC2)
unnamed: R37.2, U3.5 (DN2), U3.7 (DN1)
unnamed: R36.2, U3.6 (DP1), U3.8 (DP2)
unnamed: R49.2, U15.7 (VIA), U17.4
unnamed: R50.1, U15.6 (VOB), U17.6
unnamed: R51.1, U16.7 (VIA), U17.3
unnamed: R52.1, U16.6 (VOB), U17.1
unnamed: R31.1, U18.3 (D)
RELAY: U1.20 (IO16); also elsewhere on the board
VFO: U1.6 (IO2); also elsewhere on the board
VSS: C46.1, C49.1, J3.5, U15.8 (VDD2), U16.8 (VDD2), U17.5

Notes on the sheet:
GPIO45/GPIO46 internal Pull-down while Power up GPIO47/GPIO48 only 1.8V GPIO3 0: JTAG signal from on-chip JTAG pins 1: JTAG signal from USB Serial/JTAG controller

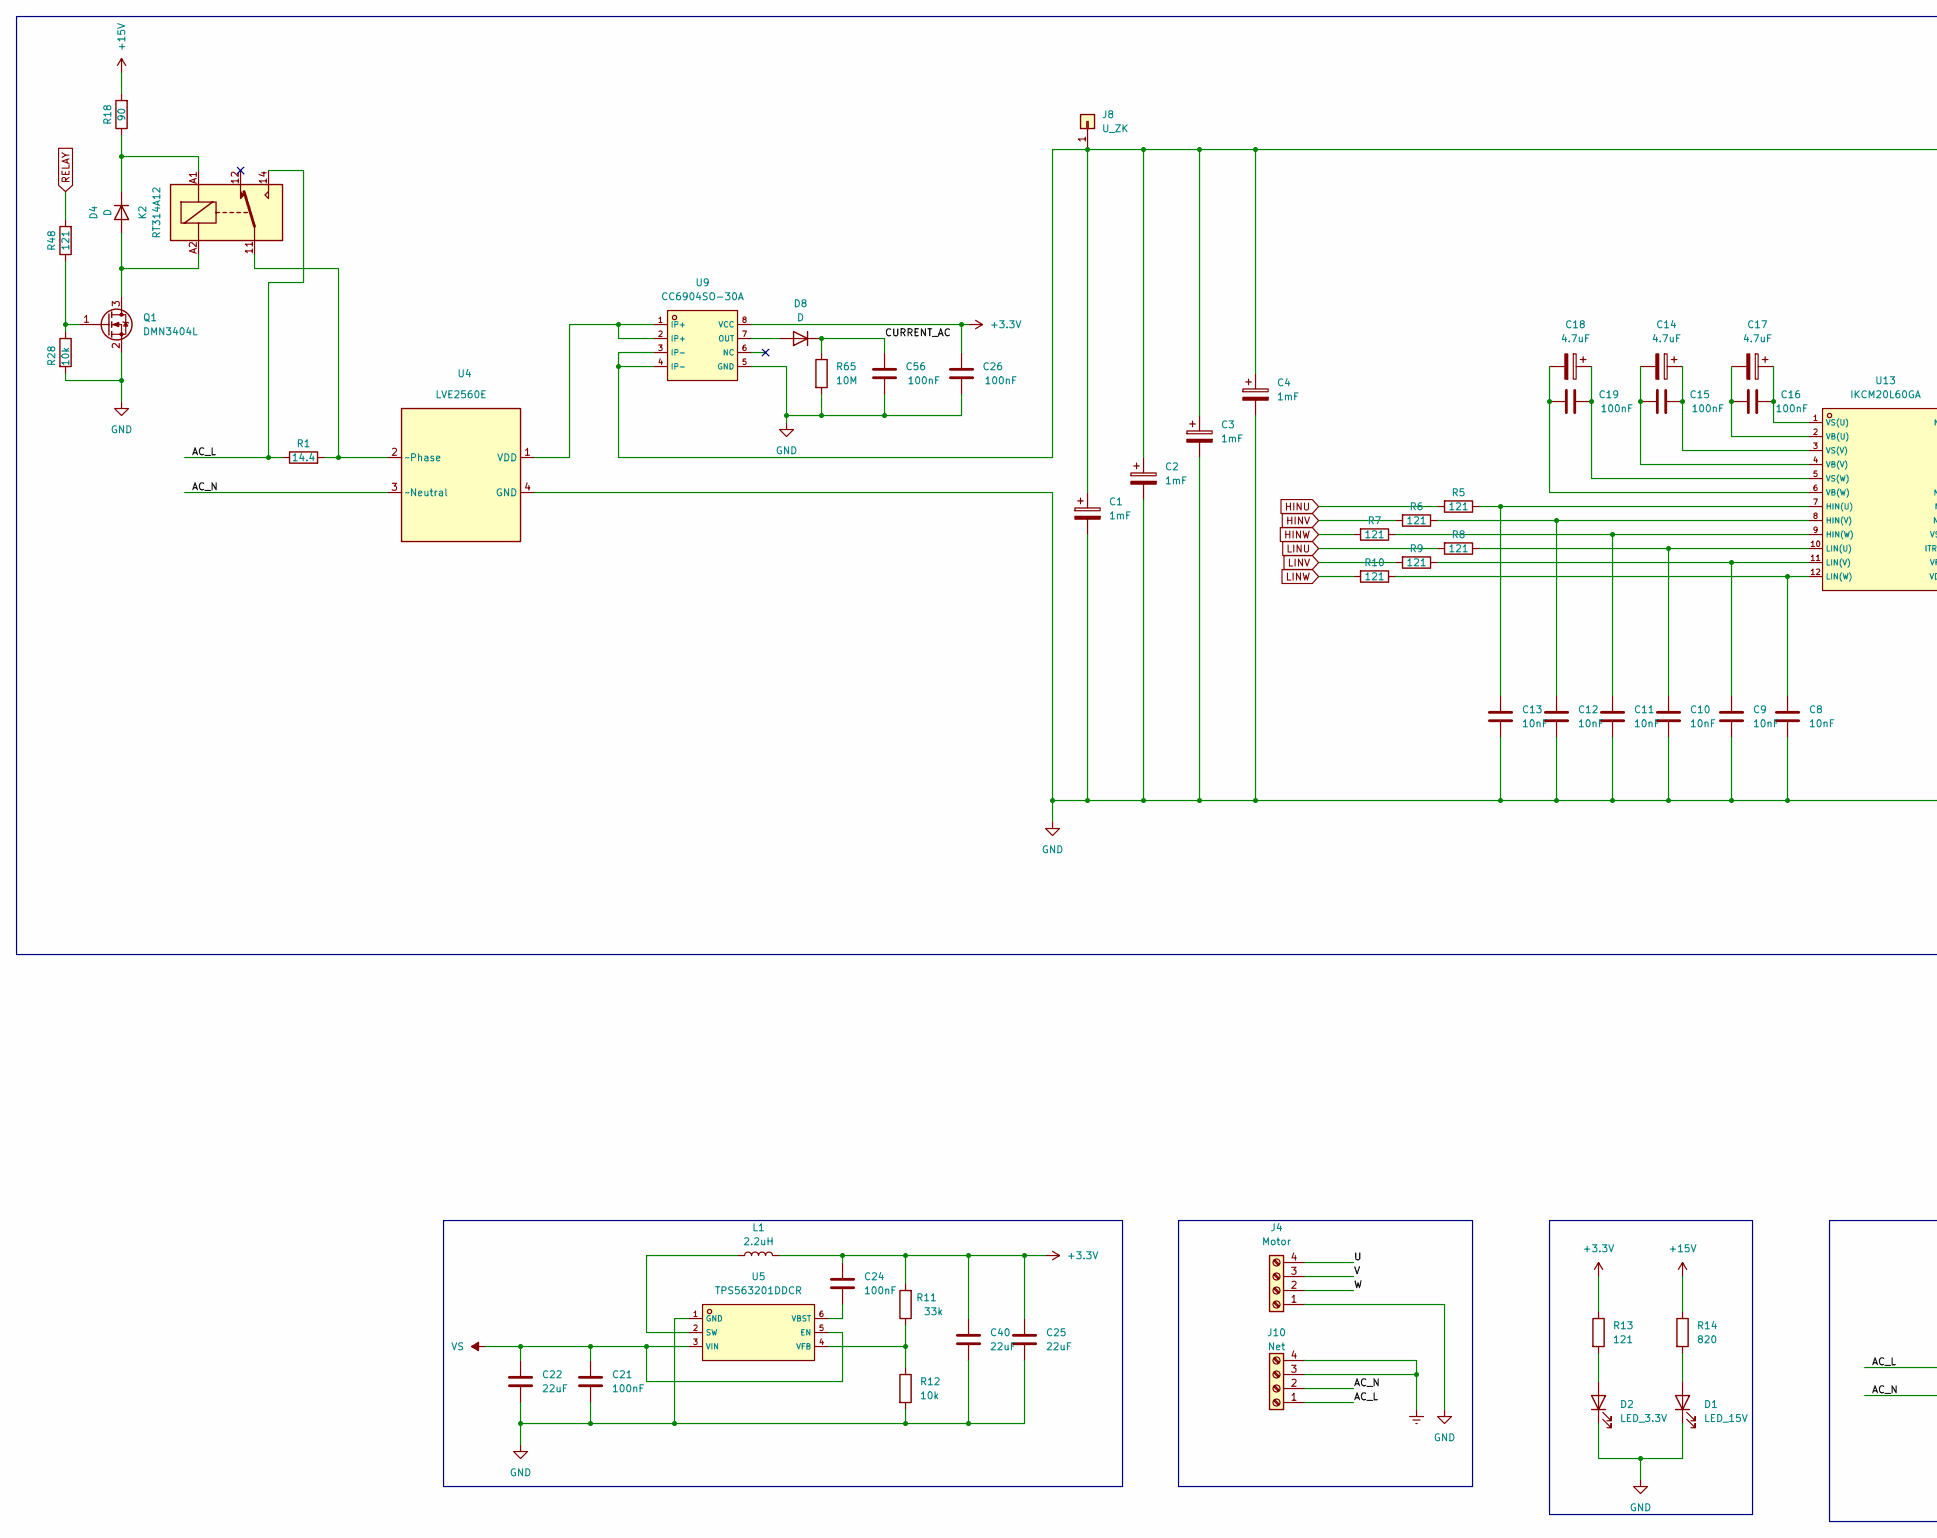
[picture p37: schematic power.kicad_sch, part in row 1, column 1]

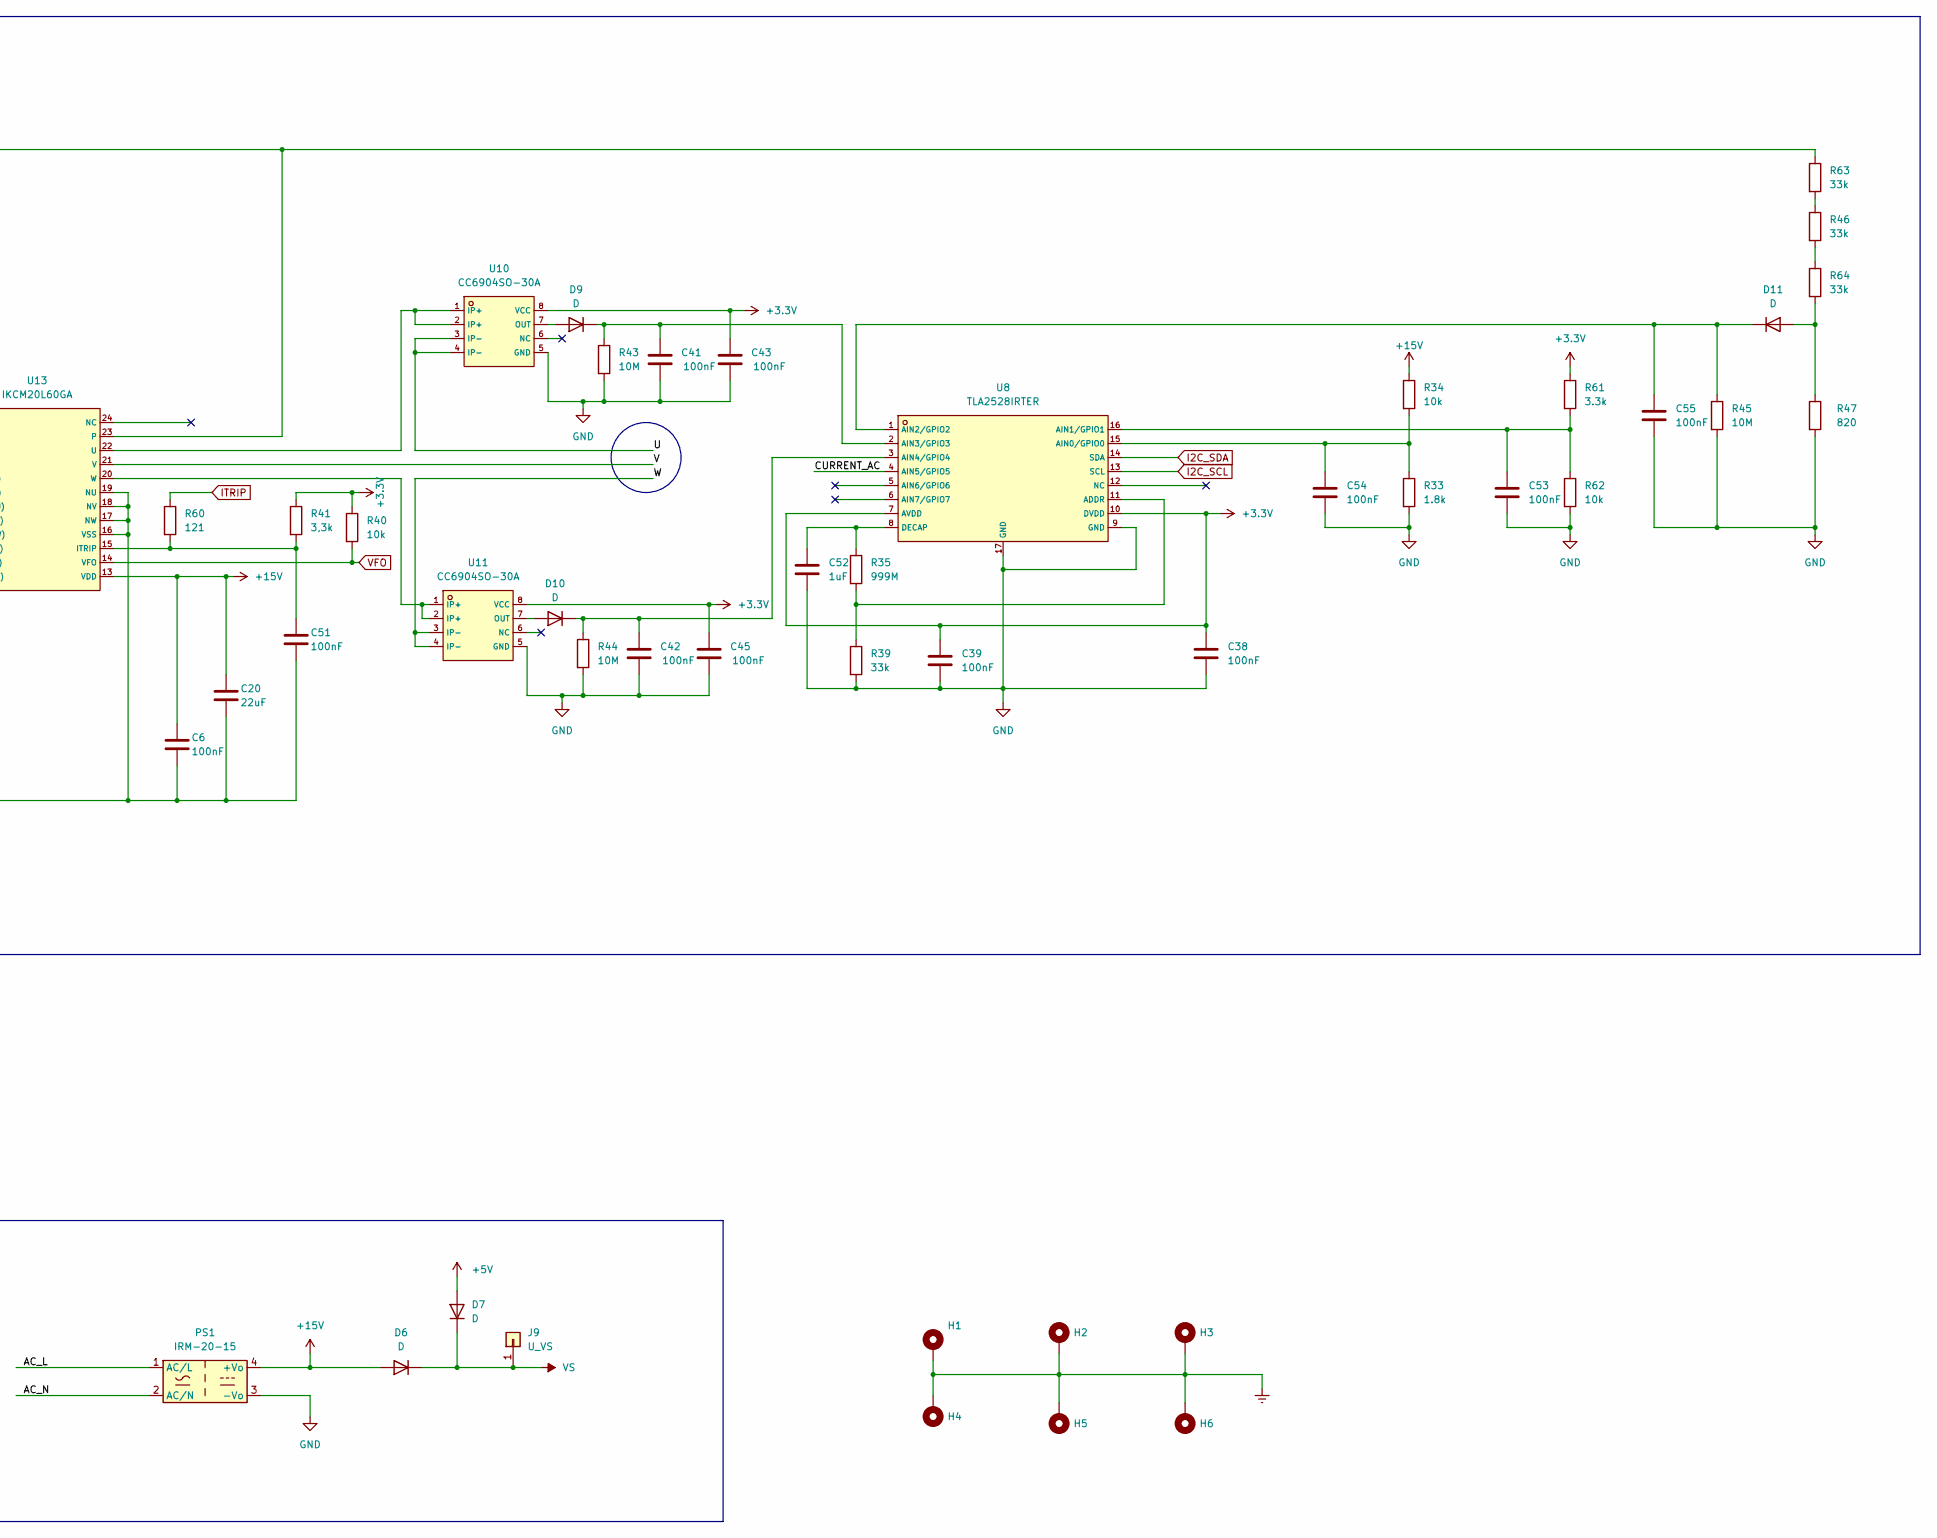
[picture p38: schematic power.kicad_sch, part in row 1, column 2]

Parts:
C1, C2, C3, C4: 1mF; ESMQ351VSN102MA50S
C6, C15, C16, C19, C21, C24, C26, C38, C39, C41, C42, C43, C45, C51, C53, C54, C55, C56: 100nF; C_0603_1608Metric
C8, C9, C10, C11, C12, C13: 10nF; C_0603_1608Metric
C14, C17, C18: 4.7uF; C_0603_1608Metric
C20, C22, C25, C40: 22uF; C_0603_1608Metric
C52: 1uF; C_0603_1608Metric
D1: LED_15V; LED_0603_1608Metric
D2: LED_3.3V; LED_0603_1608Metric
D4, D6, D7: D; D_SOD-123
D8, D9, D10, D11: D; D_0603_1608Metric
H1, H2, H3, H4, H5, H6: MountingHole_3.2mm_M3_DIN965_Pad_TopBottom
J4: Motor; TerminalBlock_Phoenix_PT-1,5-4-5.0-H_1x04_P5.00mm_Horizontal
J8: U_ZK; PinHeader_1x01_P2.54mm_Vertical
J9: U_VS; PinHeader_1x01_P2.54mm_Vertical
J10: Net; TerminalBlock_Phoenix_PT-1,5-4-5.0-H_1x04_P5.00mm_Horizontal
K2: RT314A12; Relay_SPDT_Schrack-RT1-16A-FormC_RM5mm
L1: 2.2uH; L_Bourns_SRP7028A_7.3x6.6mm
PS1: IRM-20-15; Converter_ACDC_MeanWell_IRM-20-xx_THT
Q1: DMN3404L; SOT-23
R1: 14.4; PWR220T-20
R5, R6, R7, R8, R9, R10, R13, R48, R60: 121; R_0603_1608Metric
R11, R39: 33k; R_0603_1608Metric
R12, R28, R34, R40, R62: 10k; R_0603_1608Metric
R14, R47: 820; R_0603_1608Metric
R18: 90; R_1206_3216Metric
R33: 1.8k; R_0603_1608Metric
R35: 999M; R_0603_1608Metric
R41: 3,3k; R_0603_1608Metric
R43, R44, R45, R65: 10M; R_0603_1608Metric
R46, R63, R64: 33k; R_1206_3216Metric
R61: 3.3k; R_0603_1608Metric
U4: LVE2560E
U5: TPS563201DDCR; SOT-23-6_L2.9-W1.6-P0.95-LS2.8-BL; LCSC C116592
U8: TLA2528IRTER; WQFN-16_L3.0-W3.0-P0.50-TL-EP1.7; LCSC C2866175
U9, U10, U11: CC6904SO-30A; SOP-8_L4.9-W3.9-P1.27-LS6.0-BL; LCSC C521203
U13: IKCM20L60GA; DIP-24_L36.0-W21.0-P1.60-LS28.6-TL; LCSC C536161

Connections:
+3.3V: C24.1, C25.1, C26.2, C38.2, C39.1, C40.1, C43.2, C45.2, L1.2, R11.2, R13.1, R40.1, R41.1, R61.1, U8.7 (AVDD), U8.10 (DVDD), U9.8 (VCC), U10.8 (VCC), U11.8 (VCC); also elsewhere on the board
+5V: D7.2 (A); also elsewhere on the board
+15V: C6.1, C20.1, D6.2 (A), PS1.4 (+Vo), R14.1, R18.2, R34.1, U13.13 (VDD); also elsewhere on the board
/Power/AC_L: J10.1, K2.14, PS1.1 (AC/L), R1.1
/Power/AC_N: J10.2, PS1.2 (AC/N), U4.3 (~Neutral)
/Power/CURRENT_AC: C56.2, D8.1 (K), R65.1, U8.4 (AIN5/GPIO5)
/Power/U: J4.4, U10.3 (IP-), U10.4 (IP-)
/Power/V: J4.3, U13.21 (V)
/Power/W: J4.2, U11.3 (IP-), U11.4 (IP-)
Earth: H1.1, H2.1, H3.1, H4.1, H5.1, H6.1, J10.3, J10.4
GND: C1.2, C2.2, C3.2, C4.2, C6.2, C8.2, C9.2, C10.2, C11.2, C12.2, C13.2, C20.2, C21.2, C22.2, C25.2, C26.1, C38.1, C39.2, C40.2, C41.1, C42.1, C43.1, C45.1, C51.2, C52.2, C53.2, C54.2, C55.2, C56.1, J4.1, PS1.3 (-Vo), Q1.2 (S), R12.2, R28.2, R33.2, R39.2, R43.2, R44.2, R45.2, R47.2, R62.2, R65.2, U4.4 (GND), U5.1 (GND), U8.9 (GND), U8.17 (GND), U9.5 (GND), U10.5 (GND), U11.5 (GND), U13.16 (VSS), U13.17 (NW), U13.18 (NV), U13.19 (NU); also elsewhere on the board
HINU: R5.2; also elsewhere on the board
HINV: R6.2; also elsewhere on the board
HINW: R7.2; also elsewhere on the board
I2C_SCL: U8.13 (SCL); also elsewhere on the board
I2C_SDA: U8.14 (SDA); also elsewhere on the board
ITRIP: R60.1; also elsewhere on the board
LINU: R8.2; also elsewhere on the board
LINV: R9.2; also elsewhere on the board
LINW: R10.2; also elsewhere on the board
unnamed 42: R13.2; also elsewhere on the board
unnamed: D4.1 (K), K2.A1, R18.1
unnamed: D8.2 (A), U9.7 (OUT)
unnamed: D9.2 (A), U10.7 (OUT)
unnamed: C41.2, D9.1 (K), R43.1, U8.2 (AIN3/GPIO3)
unnamed: D10.2 (A), U11.7 (OUT)
unnamed: C42.2, D10.1 (K), R44.1, U8.3 (AIN4/GPIO4)
unnamed: D11.2 (A), R47.1, R64.2
unnamed: C55.1, D11.1 (K), R45.1, U8.1 (AIN2/GPIO2)
unnamed 52: R14.2; also elsewhere on the board
unnamed: C1.1, C2.1, C3.1, C4.1, J8.1, R63.1, U9.3 (IP-), U9.4 (IP-), U13.23
unnamed: R46.1, R63.2
unnamed: R46.2, R64.1
unnamed: U4.1 (VDD), U9.1 (IP+), U9.2 (IP+)
unnamed: K2.11, R1.2, U4.2 (~Phase)
unnamed: L1.1, U5.2 (SW)
unnamed: C24.2, U5.6 (VBST)
unnamed: R11.1, R12.1, U5.4 (VFB)
unnamed: R35.2, R39.1, U8.11 (ADDR)
unnamed: C54.1, R33.1, R34.2, U8.15 (AIN0/GPIO0)
unnamed: C53.1, R61.2, R62.1, U8.16 (AIN1/GPIO1)
unnamed: C52.1, R35.1, U8.8 (DECAP)
unnamed: C13.1, R5.1, U13.7 (HIN(U))
unnamed: C12.1, R6.1, U13.8 (HIN(V))
unnamed: C11.1, R7.1, U13.9 (HIN(W))
unnamed: C51.1, R41.2, R60.2, U13.15 (ITRIP)
unnamed: C10.1, R8.1, U13.10 (LIN(U))
unnamed: C9.1, R9.1, U13.11 (LIN(V))
unnamed: C8.1, R10.1, U13.12 (LIN(W))
unnamed: U10.1 (IP+), U10.2 (IP+), U13.22 (U)
unnamed: C16.1, C17.2, U13.2 (VB(U))
unnamed: C14.2, C15.1, U13.4 (VB(V))
unnamed: C18.2, C19.1, U13.6 (VB(W))
unnamed: C16.2, C17.1, U13.1 (VS(U))
unnamed: C14.1, C15.2, U13.3 (VS(V))
unnamed: C18.1, C19.2, U13.5 (VS(W))
unnamed: U11.1 (IP+), U11.2 (IP+), U13.20 (W)
RELAY: R48.2; also elsewhere on the board
VFO: R40.2, U13.14 (VFO); also elsewhere on the board
VS: C21.1, C22.1, D6.1 (K), D7.1 (K), J9.1, U5.3 (VIN), U5.5 (EN)

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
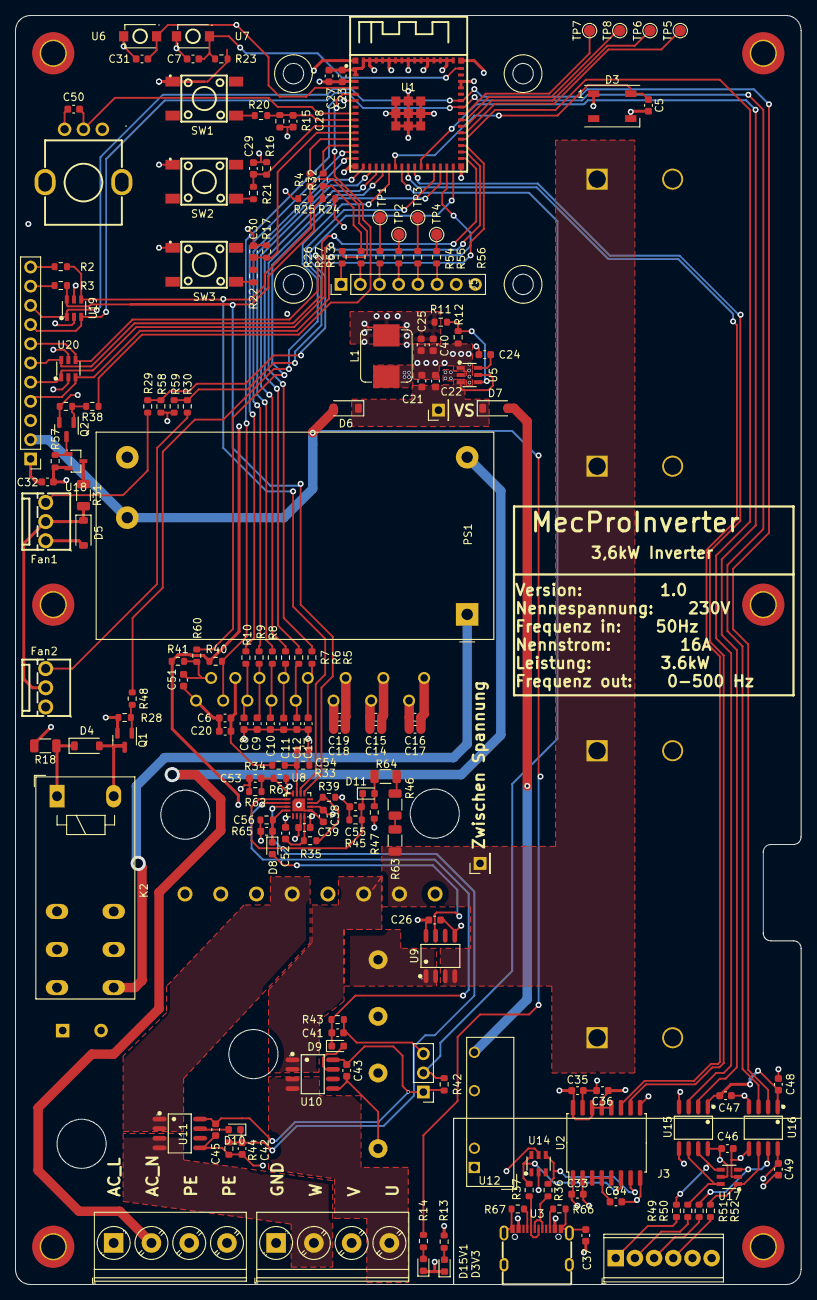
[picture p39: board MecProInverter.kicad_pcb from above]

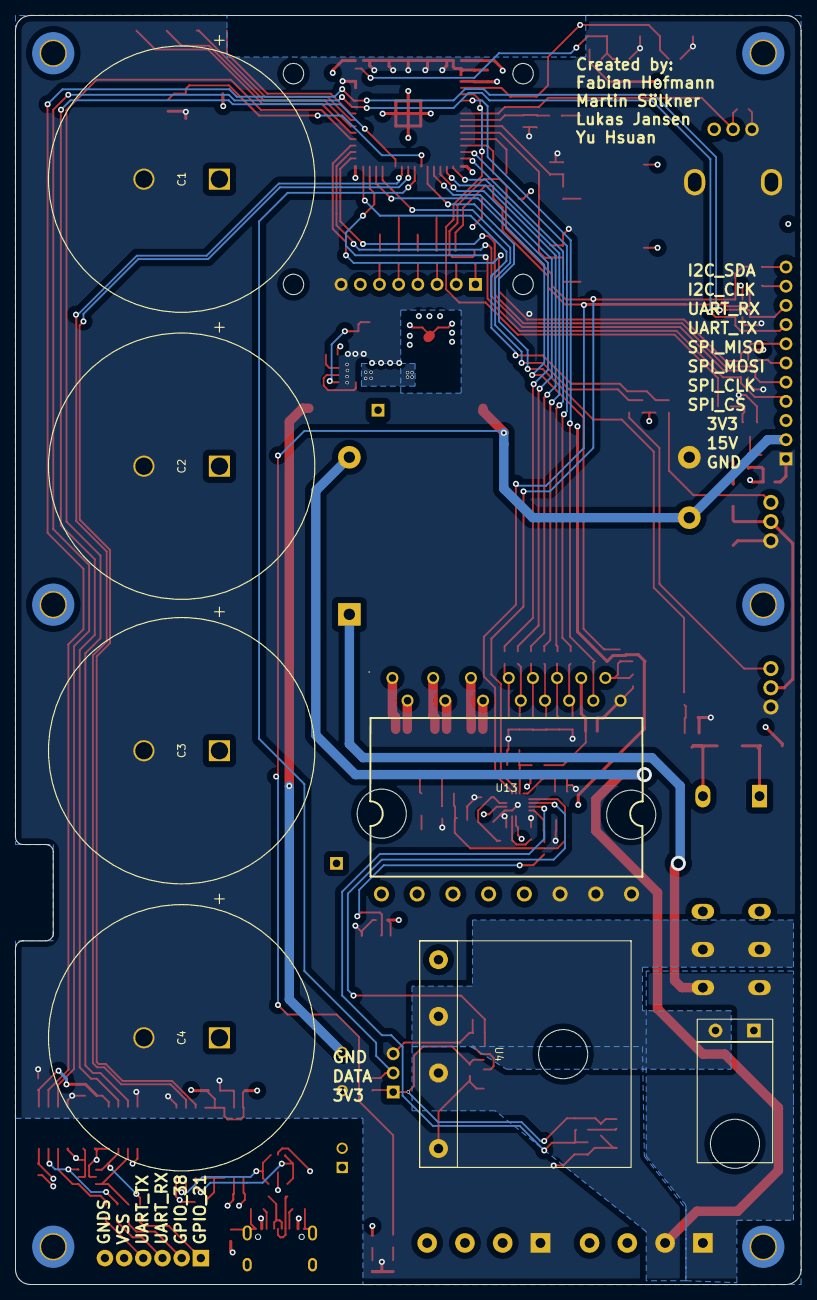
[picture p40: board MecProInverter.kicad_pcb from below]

Board: 4 copper layers, 104.0 x 168.0 mm, 186 parts (7 on the bottom side), 129 nets.

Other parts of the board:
D3V3: LED_3.3V; LED_0603_1608Metric
D15V1: LED_15V; LED_0603_1608Metric
Q2: DMN3404L; SOT-23

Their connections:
GND: D3V3.1 (K), D15V1.1 (K), Q2.2 (S); also elsewhere on the board
unnamed 42: D3V3.2 (A); also elsewhere on the board
unnamed 52: D15V1.2 (A); also elsewhere on the board

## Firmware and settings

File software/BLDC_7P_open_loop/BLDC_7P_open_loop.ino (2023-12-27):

#include <SimpleFOC.h>

#define 




#define PIN_IPH1 15 //ADC2_5 == A15
#define PIN_IPH2 16 //ADC2_6 == A16 
#define PIN_IPH3 17 //ADC2_7 == A17

#define HALL_PH1 19 
#define HALL_PH2 18 
#define HALL_PH3 5

#define PIN_PH1_H 1 //23
#define PIN_PH2_H 2 //1
#define PIN_PH3_H 3
#define PIN_PH1_L 4
#define PIN_PH2_L 5
#define PIN_PH3_L 6

#define CURRENT_SENSE_GAIN -40.633
#define NBR_POLE_PAIRS 7




MagneticSensorI2C as5600 = MagneticSensorI2C(AS5600_I2C);
BLDCDriver6PWM driver = BLDCDriver6PWM(PIN_PH1_H, PIN_PH1_L, PIN_PH2_H, PIN_PH2_L, PIN_PH3_H, PIN_PH3_L);
InlineCurrentSense current_sense  = InlineCurrentSense(1, CURRENT_SENSE_GAIN, PIN_IPH1, PIN_IPH2, PIN_IPH3);
BLDCMotor motor = BLDCMotor(NBR_POLE_PAIRS);


int adcValue1;
int adcValue2;
int adcValue3;
uint8_t hall_sensor_state;

void setup() {
  // monitoring port
  Serial.begin(115200);
  Serial.print("[INFO] Serial begin.");

  // init magnetic sensor hardware
  //as5600.init();

  pinMode(PIN_IPH1, INPUT);
  pinMode(PIN_IPH2, INPUT);
  pinMode(PIN_IPH3, INPUT);

  pinMode(HALL_PH1, INPUT);
  pinMode(HALL_PH2, INPUT);
  pinMode(HALL_PH3, INPUT);
  
  pinMode(PIN_PH1_H, OUTPUT);
  pinMode(PIN_PH2_H, OUTPUT);
  pinMode(PIN_PH3_H, OUTPUT);
  pinMode(PIN_PH1_L, OUTPUT);
  pinMode(PIN_PH2_L, OUTPUT);
  pinMode(PIN_PH3_L, OUTPUT);
 
  digitalWrite(PIN_PH1_H, LOW);
  digitalWrite(PIN_PH2_H, LOW);
  digitalWrite(PIN_PH3_H, LOW);
  digitalWrite(PIN_PH1_L, LOW);
  digitalWrite(PIN_PH2_L, LOW);
  digitalWrite(PIN_PH3_L, LOW);

  Serial.print("[INFO] Pin init.");

  driver.pwm_frequency = 20000;
  driver.dead_zone = 0.05;
  driver.voltage_power_supply = 12;
  driver.voltage_limit = 12;
  Serial.print("[INFO] Driver init.");
  driver.init();
  Serial.print("[INFO] Init fertig.");
  driver.enable();
  //current_sense.init();
  motor.linkDriver(&driver);

  motor.voltage_limit = 3;   // [V]
  motor.velocity_limit = 90; // [rad/s] cca 50rpm
 
  // open loop control config
  motor.controller = MotionControlType::velocity_openloop;
  motor.init();
_delay(1000);
    
}

void loop() {
  Serial.print("[INFO] Loop start.");
  motor.move(40);

  
  // display the angle and the angular velocity to the terminal
  /*Serial.print("Angle[rad]: ");
  Serial.print(as5600.getAngle());
  Serial.print("\t Speed [rad/s]:");
  Serial.println(as5600.getVelocity());


  currents = current_sense.getPhaseCurrents();
  Serial.print("Current Ph1 [mA]: ");
  Serial.println(currents.a*1000);
  Serial.print("Current Ph2 [mA]: ");
  Serial.println(currents.b*1000);
  Serial.print("Current Ph3 [mA]: ");
  Serial.println(currents.c*1000);
  Serial.println("");*/
  
}

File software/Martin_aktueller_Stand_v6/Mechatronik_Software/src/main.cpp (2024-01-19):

//#include "main.hpp"
#include <Arduino.h>
#include <stdlib.h>
#include <stdio.h>
#include <Wire.h>
#include <Adafruit_SSD1306.h>
#include <Adafruit_GFX.h>
#include "conf.hpp"

// Objekt-Declaration that it is seeable, by the loop

#ifdef PWM_TEST

#include "foc_pwm.hpp"
#define FREQUENZ 10

BLDCDriver6PWM*driver;
BLDCMotor*motor;

void setup()
{

  Serial.begin(115200);
  FOC::init(&driver,&motor);
  Serial.println("Test");
   //FOC::init(driver,motor);
  Serial.println("Test");
}

void loop()
{
  //USBSerial.print(".");
  FOC::PWM_Generation(motor,2*PI*FREQUENZ);
}

#endif

#ifdef MEASURE_PRE_CHARGE
#include "state_machine.hpp"
State_Machine fsm;

void setup()
{
  Serial.begin(115200);
}

void loop()
{
  /*  while Schleife der Routine  */
  fsm.Update();
}

#endif
#ifdef ADC_TEST
#include "sensor_func.hpp"
#define I2C_SDA 8
#define I2C_SLK 9

TwoWire*twowire=new TwoWire(BUS_NUM);
uint8_t ergebnis;
void setup()
{
  USBSerial.begin(115200);
  twowire->begin(I2C_SDA,I2C_SLK);
  ergebnis=TLA2528::StartUp_TLA2528(twowire);
}

void loop()
{
  USBSerial.println(ergebnis);
  TLA2528::man_CHA_Read(twowire,V_15);
}
#endif

#ifdef TEMP_TEST
#include "sensor_func.hpp"
OneWire*onewire=new OneWire(ONE_WIRE_PIN);
DallasTemperature*temp=new DallasTemperature(onewire);

void setup()
{
  Serial.begin(115200);
  temp->begin();
}

void loop()
{
  float ergebnis=MAX31820::readTemperature(*temp);
  Serial.println(ergbnis);
}
#endif

#ifdef TIMING
#include "foc_pwm.hpp"
void setup()
{
  Serial.begin(115200);
  // Set timer frequency to 1Mhz
  TIMING::initTimer(1000000);
  delay(3000);
  TIMING::startTimer();
  delay(5000);
  Serial.println(flag);
  TIMING::stopTimer();
  flag=false;
  delay(2000);
}

  

void loop()
{
  Serial.println(flag); 
}


#endif

#ifdef WHOLE_TEST
#include "state_machine.hpp"
State_Machine fsm;

void setup()
{
  Serial.begin(115200);
}

void loop()
{
  /*  while Schleife der Routine  */
  fsm.Update();
  fsm.Transition(Check_Ok);
}

#endif
/*********************************************************************************************************
Plan B falls das in einer Klasse nicht funktioniert:

// aus Zeitgründen soll nur ein flag übergeben werden, aus Zeitgründen
volatile uint8_t flag;

// Definition of the Callback Function
// IRAM put it into RAM for faster Execution
void IRAM_ATTR timer_isr_callback(void*arg) {
  // Umcastung von den void arg, da nur void übergeben werden darf
  Interface* inte=static_cast<Interface*>(arg);
  inte->flag
  flag=true;
}

void setup()
{
  // Übergabe der Argumente für den Interrupt
  //  * callback: Name der ISR Funktion
  //  * arg: Übergabe der argumentde, in dem Fall dem Interface
  //  * name: Name der callback Funktion

  const esp_timer_create_args_t periodic_timer_args = {
    .callback = &timer_isr_callback,
    .arg=fsm.getInterface(),  //Aufruf einer static function
    .name = "periodic"
  };

  // Erstellung einer Instanz
  esp_timer_handle_t periodic_timer;

  // Erstellung des Timers
  esp_timer_create(&periodic_timer_args,&periodic_timer);

  // Setzen der Periode
  esp_timer_start_periodic(periodic_timer,1000000/TIMER_FREQUENCY_HZ);

  // Setzen des Stops
  //esp_timer_stop(periodic_timer);
  
  Serial.begin(115200);
}
*********************************************************************************************************/

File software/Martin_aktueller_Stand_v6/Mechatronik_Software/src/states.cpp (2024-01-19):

#include "states.hpp"

/**************************************************************************************************************************************
* POWER_UP
Anmerkungen:
PROGMEM auch zu ESP32 exportiert
temp.begin() besitzt keinen Rückgabewert
**************************************************************************************************************************************/
void Power_Up::enter(State_Machine* pOwner, Interface* interface)
{
  // Initialisierungen der Sinus_Tabelle
  PROGMEM Sin_Gen::Sin_Tab();

  //Initialisierung der Switch_Assembly
  pinMode(SW1,INPUT);
  pinMode(SW2,INPUT);
  pinMode(SW3,INPUT);

  //Initialisierungen der BUS-Systeme
  interface->oneWire=new OneWire(ONE_WIRE_PIN);
  interface->twoWire=new TwoWire(BUS_NUM);

  // Intitialisierungen_Sensorik
  interface->temp=new DallasTemperature(interface->oneWire);
  interface->temp->begin();

}

void Power_Up::Execute(State_Machine* pOwner,Interface* interface)
{
  // Referenzen, zur Vereinfachung
  auto &twoWire=interface->twoWire;
  auto &oneWire=interface->oneWire;
  auto &display=interface->display;
  auto &temp=interface->temp;
  // Check of the I2C Bus (nicht möglich für den OneWire Bus)
  interface->error_flag_per += (twoWire->begin(I2C_SDA,I2C_SLK))  ? 0 : 1;

  // Definitionen aller I2C-Bus Definitionen erst danach, da begin Funktionen erst danach aufgerufen
  interface->display=new Adafruit_SSD1306(SCREEN_WIDTH, SCREEN_HEIGHT, interface->twoWire, -1); // Der -> hat eine höhere Prio als &

  //Check bzw. erste Kommunikation
  interface->error_flag_per+= (temp->getDeviceCount()>0) ? 0 : 1;
  interface->error_flag_per+= (display->begin(SSD1306_SWITCHCAPVCC, 0x3C,true,false)) ? 0 : 1;  // Mit dem letzten false teilt man dem Konstruktor mit, dass ein begin schon initialisiert wurde, bei dem I2C Bus
  
  // State Transition
  //if(interface->error_flag_per>0)  { pOwner->Transition(failure); } else { pOwner->Transition(Check_Ok); }
  Serial.println("Power_Up");
  pOwner->Transition(Check_Ok);
}
void Power_Up::exit(State_Machine* pOwner, Interface* interface)
{

}

/**************************************************************************************************************************************
* PRE_CHARGE
* Anmerkungen: pinMode fürs Relay hier definiert,
* sollte aber pasen da loop auch nur einmal aufgerufen und anschließend verlassen wird
* static last timestamp: falls man nochmal in die Funktion reingeht
**************************************************************************************************************************************/
void Pre_Charge::enter(State_Machine* pOwner, Interface* interface)
{
  //pinMode/digitalWrite
  pinMode(RELAY_SHUNT_AC,OUTPUT);
  pinMode(I_TRIP,OUTPUT);
  digitalWrite(RELAY_SHUNT_AC,LOW);
  digitalWrite(I_TRIP,HIGH);
  
}

void Pre_Charge::Execute(State_Machine* pOwner, Interface* interface)
{  
  //Logik
  unsigned long last_timestamp=0;
  while(V_TANK_VOLTAGE_THRES>=V_TANK_CALC*TLA2528::man_CHA_Read(interface->twoWire,V_TANK))
  {
    //Timeout
    if ((millis()-last_timestamp)>=10000)
    {
      pOwner->Transition(failure);
      return;
    }
    last_timestamp=millis();
  }
  digitalWrite(RELAY_SHUNT_AC,HIGH);
  pOwner->Transition(U_Ok);
  Serial.println("State_Pre_Charge");
}

void Pre_Charge::exit(State_Machine* pOwner, Interface* interface)
{

}

/**************************************************************************************************************************************
* STANDBY
**************************************************************************************************************************************/
void Standby::enter(State_Machine* pOwner, Interface* interface)
{
  //interface->timing=new Timing();
  //interface->timing->start(VELOCITY_LIMIT);
}
void Standby::Execute(State_Machine* pOwner, Interface* interface)
{  
  //Entprellsoftware
  Serial.println("Standby");
  if(digitalRead(SW1)) pOwner->Transition(On_Switch);
}
void Standby::exit(State_Machine* pOwner, Interface* interface)
{

}

/**************************************************************************************************************************************
* RUN
**************************************************************************************************************************************/
void Run::enter(State_Machine* pOwner, Interface* interface)
{
  //FOC::init(interface->driver,interface->motor);
  analogReadResolution(ADC_RESOLUTION);
}
void Run::Execute(State_Machine* pOwner, Interface* interface)
{
  if(!digitalRead(SW1))
  {
    float new_target_value=POTI_FKT::Read_Out_Frequency(POT1,ADC_RESOLUTION,VELOCITY_LIMIT);
    FOC::PWM_Generation(interface->motor,new_target_value);

  }
  else
  {
    pOwner->Transition(Off_Switch);
  }
}
void Run::exit(State_Machine* pOwner, Interface* interface)
{

}

/**************************************************************************************************************************************
* SAFESTATE
**************************************************************************************************************************************/
void Safestate::enter(State_Machine* pOwner, Interface* interface)
{
  digitalWrite(RELAY_SHUNT_AC,LOW);
  digitalWrite(I_TRIP,HIGH);
}
void Safestate::Execute(State_Machine* pOwner, Interface* interface)
{
  //hier eventueller Check das alles Ok und manuelle Freigabe für den Controller
}
void Safestate::exit(State_Machine* pOwner, Interface* interface)
{

}

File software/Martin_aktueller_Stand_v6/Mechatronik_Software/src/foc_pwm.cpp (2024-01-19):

#include "foc_pwm.hpp"

using namespace FOC;

/**************************************************************************************************************************************
* Bereich für die Field Oriented Controll
**************************************************************************************************************************************/
void FOC::init(BLDCDriver6PWM** driver,BLDCMotor** motor)
{
    *driver = new BLDCDriver6PWM(HINW, LINW, HINV, LINV, HINU, LINU);
    *motor = new BLDCMotor(POLE_PAIR);
    pinMode(LINW,OUTPUT);
    pinMode(HINW,OUTPUT);
    pinMode(LINV,OUTPUT);
    pinMode(HINV,OUTPUT);
    pinMode(HINU,OUTPUT);
    pinMode(HINU,OUTPUT);
    digitalWrite(LINW, LOW);
    digitalWrite(HINW, LOW);
    digitalWrite(LINV, LOW);
    digitalWrite(HINV, LOW);
    digitalWrite(HINU, LOW);
    digitalWrite(HINU, LOW);

    // Driver-Part
    (*driver)->pwm_frequency = PWM_FREQUENCY;
    (*driver)->dead_zone = DEAD_ZONE;
    (*driver)->voltage_power_supply = VOLTAGE_POWER_SUPPLY;
    (*driver)->voltage_limit = D_VOLTAGE_LIMIT;
    (*driver)->init();
    //driver->enable(); //waere glaube ich ohne motor

    // Motor-Part
    (*motor)->linkDriver(*driver);
    (*motor)->voltage_limit = M_VOLTAGE_LIMIT;   // [V]
    (*motor)->velocity_limit = (float) 2*PI*VELOCITY_LIMIT; // [rad/s] cca 50rpm
    (*motor)->controller = MotionControlType::velocity_openloop;   // open loop control config
    (*motor)->init();
    _delay(1000);
}

void FOC::PWM_Generation(BLDCMotor* motor, float freq)
{
    static float new_target_value=2*PI*freq;
    motor->move(new_target_value);
}

/**************************************************************************************************************************************
* Bereich für die Timing Function

Anmerkungen: 
* static Timing*instance: Globaler Zeiger auf die Timing Instanz, da so die ISR aufgerufen werden kann
* nur eine Timing Klasse erstellen
**************************************************************************************************************************************/
volatile uint64_t flag_isr = 0;

void IRAM_ATTR onTimer()
{
  flag_isr++;
}

namespace TIMING
{
hw_timer_t * timer_p;
void initTimer(uint64_t us_frequenz)
{
  timer_p = timerBegin(0, 80, true);
  timerAttachInterrupt(timer_p, &onTimer, true);
  timerAlarmWrite(timer_p, us_frequenz, true);
}

void startTimer()
{
  timerAlarmEnable(timer_p);
}

void stopTimer()
{
  timerAlarmDisable(timer_p);
}

void destructTimer()
{
  timerEnd(timer_p);
}
}

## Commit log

2023-10-19 init
    init
    [MecProInverter.kicad_pcb, MecProInverter.kicad_sch]
2023-10-24 documentation
    added bestellliste
    [MecProInverter_Bestellliste.xlsx]
2023-10-26 docu
    Projektplan
    [MecProInverter_Bestellliste.xlsx, MecProInverter_Projektplan.xlsx]
2023-11-02 docu
    ssd1306 in software verschoben
    [MecProInverter_Bestellliste.xlsx]
2023-11-04 electronic
    library added
    [MecProInverter.kicad_pcb, MecProInverter.kicad_sch, MecProInverter_Bestellliste.xlsx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]
2023-11-04 electronic
    Test .gitignore (venv)
    [MecProInverter.kicad_sch, power.kicad_sch]
2023-11-05 electronic
    library expanded
    [BOM.xlsx, MecProInverter.kicad_pcb, MecProInverter.kicad_sch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]
2023-11-07 electronic
    - power: added 3.3V coverter
    - power: added bridge rectifier
    - power: added half bridge
    [control.kicad_sch, power.kicad_sch]
2023-11-10 electronic
    -power: added 15/3,3 Volt voltage regulator
    - power: added power relay
    - control: added USB-ISO, added User interface
    [MecProInverter.kicad_pcb, MecProInverter_Bestellliste.xlsx, control.kicad_sch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]
2023-11-17 FSM
    Funktionierende Klasse für eine State Machine:
    TState_Machine: allgemeines Template für eine FSM
    states: States die benutzt werden
    state_machine: Spezialisierung
2023-11-20 electronic
    -Control: Added Temp, Fan,
    [MecProInverter_Bestellliste.xlsx, control.kicad_sch]
2023-11-24 electronic
    Added: current sensor
    [MecProInverter.kicad_pcb, MecProInverter_Bestellliste.xlsx, control.kicad_sch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]
2023-11-28 Electronic
    Currentsensor updated
    Power structure updated
    [MecProInverter_Bestellliste.xlsx, control.kicad_sch, power.kicad_sch]
2023-11-29 Electronic
    Rework: Fan, ESP32 Pinout, 15V Power,
    Added: GPIO ISO, ESD
    [MecProInverter.kicad_pcb, control.kicad_sch, power.kicad_sch]
2023-11-29 Electronic
    Power Terminal edit
    [MecProInverter.kicad_pcb, MecProInverter_Bestellliste.xlsx, control.kicad_sch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]
2023-11-30 Electronic
    Footprint assignment
    [MecProInverter.kicad_pcb, MecProInverter_Bestellliste.xlsx, control.kicad_sch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]
2023-11-30 Electronic
    Voltage messurment updated
    [MecProInverter.kicad_pcb, MecProInverter_Bestellliste.xlsx, control.kicad_sch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]
2023-11-30 Electronic
    docu
    [BrueckenGR_LVE2560E.stp, Cap.stp, MecProInverter.kicad_pcb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]
2023-12-04 Electronic
    Added 3d Moodel on Layout
    [MecProInverter.kicad_pcb, MecProInverter_Bestellliste.xlsx, control.kicad_sch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]
2023-12-06 Electronic
    Schematic V1.0
    [MecProInverter.kicad_pcb, MecProInverter_Bestellliste.xlsx, control.kicad_sch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]
2023-12-06 Electronic
    Added USB-C CC Resistor
    [MecProInverter.kicad_pcb, control.kicad_sch]
2023-12-07 Electronic
    Layout begin
    [MecProInverter.kicad_pcb, control.kicad_sch]
2023-12-07 Electronic
    Generated Step
    [MecProInverter-B_Cu.gbr, MecProInverter-B_Mask.gbr, MecProInverter-B_Paste.gbr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]
2023-12-07 Electronic
    Ready to buy
    [MecProInverter-B_Cu.gbr, MecProInverter-B_Mask.gbr, MecProInverter-B_Paste.gbr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]
2023-12-13 Electronic
    PCB buy!!!
    [MecProInverter-B_Cu.gbr, MecProInverter-B_Mask.gbr, MecProInverter-B_Silkscreen.gbr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]
2023-12-21 New Version
    Implement the sensor namespace to readout the ADC and temp
2023-12-27 Software
    Added Pinout
    Created arduino Hardware Test
    [control.kicad_sch]
2024-01-11 Software
    Added LED
2024-01-11 Software
    Added ADC Test
    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
2024-01-23 Projektberichte
    Elektronik added
    [Fuehrung_Taster.stl, Poti_Verlaengerung.stl, control.kicad_sch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]
